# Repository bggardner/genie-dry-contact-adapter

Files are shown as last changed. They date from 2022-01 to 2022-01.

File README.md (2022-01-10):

# genie-dry-contact-adapter
Push-Button Adapter for Series III Compatible Genie Garage Door Openers

KiCAD project for a clone of the [Genie Series III Dry Contact Adapter](https://store.geniecompany.com/products/series-iii-dry-contact-adapter-switch)

# Background
After purchasing a Wifi controller for my garage door opener, I realized that my opener did not have a standard push-button ("dry contact") input.
I investigated how my existing [wall console](https://store.geniecompany.com/products/copy-of-wall-console-for-series-ii-product) operated and discovered that it provided three different signals depending on the button that was pushed (DOOR, LIGHT, or LOCK).
The opener provides a soft ~15V to the wall console, and the wall console shorts this signal at a low duty cycle (~10%).  The approximate frequency for each button is as follows:
* DOOR: 16kHz
* LIGHT: 8kHz
* LOCK: 4kHz

The opener detects the frequency of the short and is able to determine which button is pressed.
I was only interested in the DOOR signal, so I simplified the circuit, but a full schematic of the wall console is provided for convenience.
I also discovered that the wall console itself was a dry contact adapter, as it had two-through hole pads in the circuit board that were in parallel with the DOOR button.

# Fabrication
While I initially breadboarded the circuit, I wanted a PCB.
Using [JLCPCB](https://jlcpcb.com), I was able to get five populated/assembled boards delivered for less than $20, not including the [screw terminals](https://www.amazon.com/gp/product/B07H5G7GC6), which I installed myself.
That is much less than a single ~$50 adapter (or ~$30 wall console) sold by Genie, especially given that I have two garage doors.

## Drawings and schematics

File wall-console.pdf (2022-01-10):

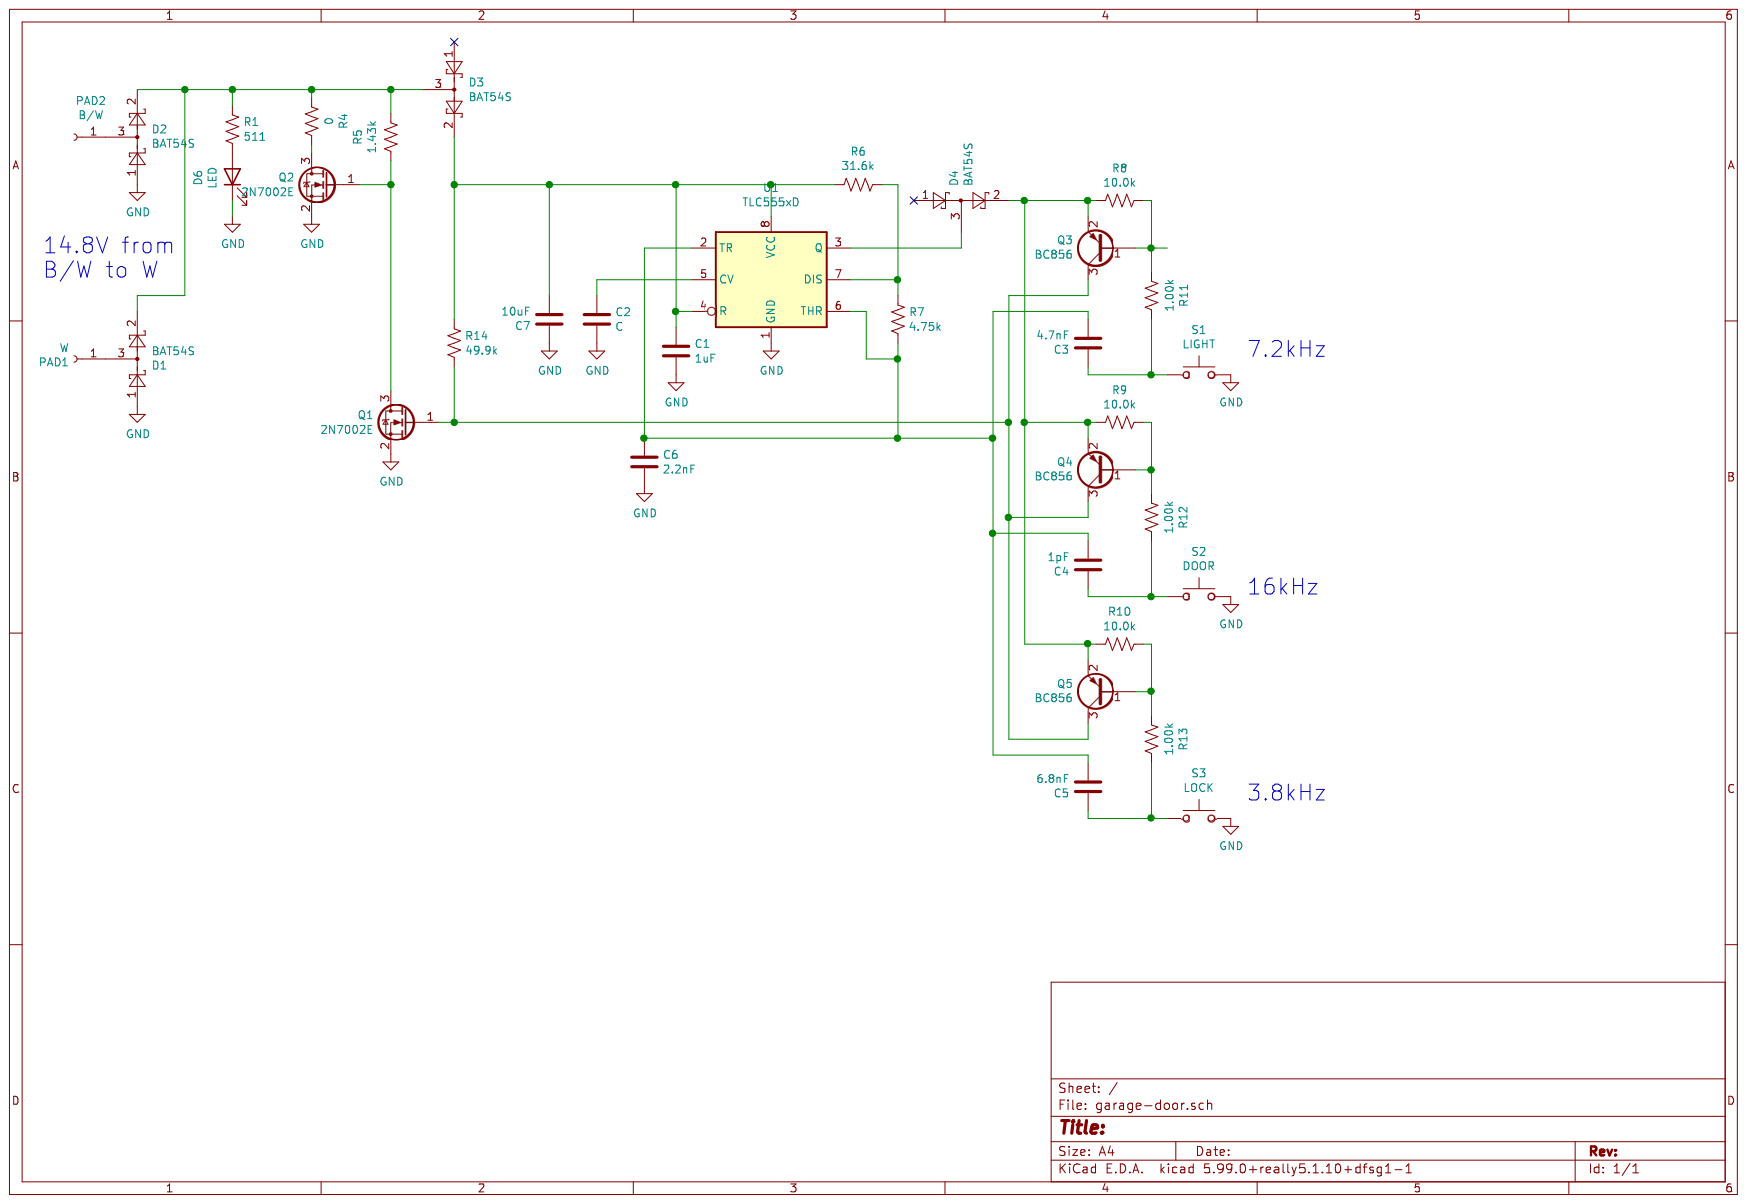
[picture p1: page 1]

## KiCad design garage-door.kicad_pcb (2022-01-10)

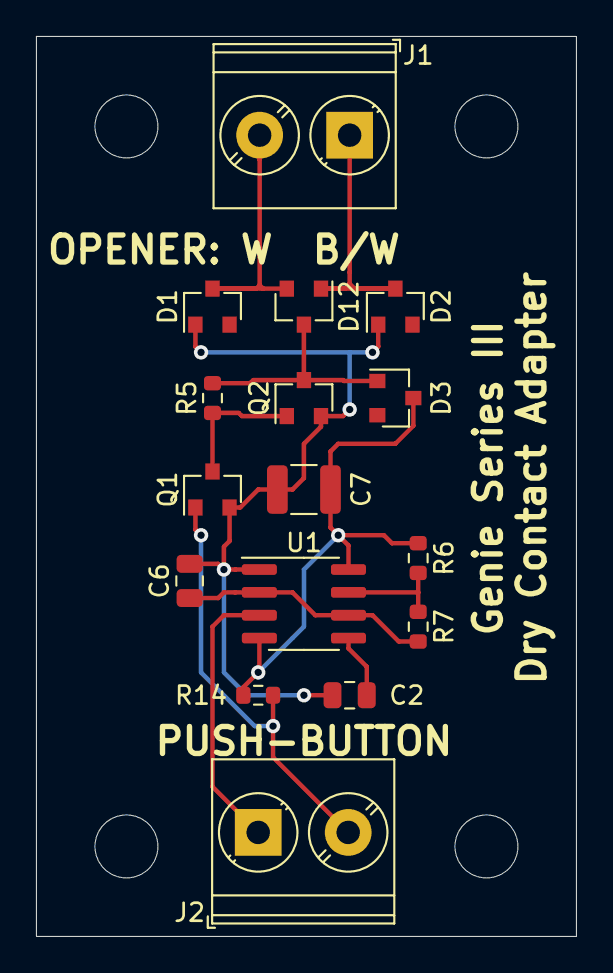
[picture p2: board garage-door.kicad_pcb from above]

Board: 2 copper layers, 30.0 x 50.0 mm, 20 parts (0 on the bottom side), 11 nets.

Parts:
C2: 0.1uF; C_0805_2012Metric
C6: 1nF; C_0805_2012Metric
C7: 10uF; C_1210_3225Metric
D1, D2, D3, D12: BAT54C; SOT-23
H1, H2, H3, H4: MountingHole; MountingHole_3.5mm
J1: OPENER; TerminalBlock_Phoenix_PT-1,5-2-5.0-H_1x02_P5.00mm_Horizontal
J2: REMOTE; TerminalBlock_Phoenix_PT-1,5-2-5.0-H_1x02_P5.00mm_Horizontal
Q1, Q2: 2N7002; SOT-23
R5: 1.5k; R_0603_1608Metric
R6: 68k; R_0603_1608Metric
R7: 10k; R_0603_1608Metric
R14: 56k; R_0603_1608Metric
U1: NE555DR; SOIC-8_3.9x4.9mm_P1.27mm

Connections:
GND: C2.2, C6.2, C7.1, D1.1, D2.1, Q1.2, Q2.2, U1.1
unnamed: C2.1, U1.5
unnamed: C6.1, R7.2, U1.2, U1.6
unnamed: C7.2, D3.3, R6.1, R14.1, U1.4, U1.8
unnamed: D1.3, D12.2, J1.2
unnamed: D2.3, D12.1, J1.1
unnamed: D3.1, D12.3, Q2.3, R5.2
unnamed: J2.1, U1.3
unnamed: J2.2, Q1.1, R14.2
unnamed: Q1.3, Q2.1, R5.1
unnamed: R6.2, R7.1, U1.7
